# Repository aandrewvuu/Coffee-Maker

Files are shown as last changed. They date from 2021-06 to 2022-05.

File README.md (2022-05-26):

# Coffee Maker

As avid coffee consumers, we always wanted to try different techniques to make my coffee. Combining our love for coffee and my passion for engineering, we sought to automate pour over techinque to consistently create a delicious and flavourful coffee. This readme will act as a step by step guide as well as share our thought process while tackling this project.

## Preliminary Brainstorming

This is a brief overview of the logic behind this:

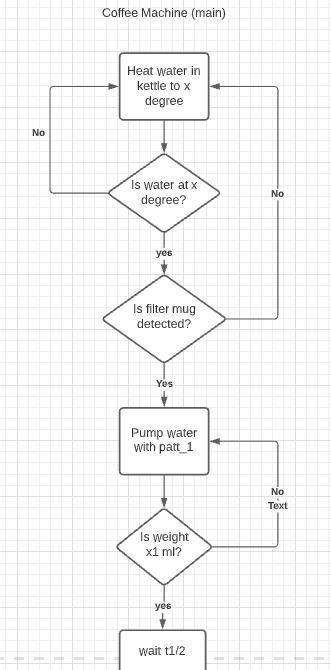
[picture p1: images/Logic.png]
 

This is a basic wiring diagram:

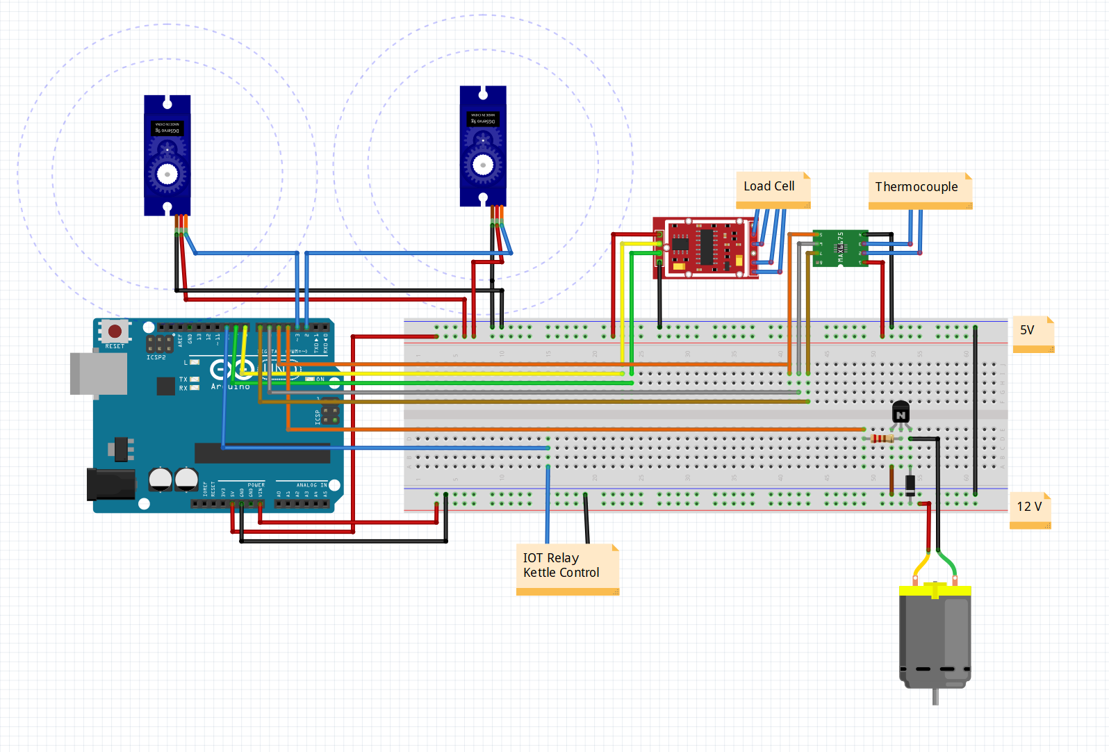
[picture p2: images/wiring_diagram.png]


## Bill of Materials

| Item | Amount | 
| -----|---|
|Arduino|1|
|IoT Relay|1|
|Pump|1|
|Kettle|1|
|Thermocouple|1|
|Load cell|1|
|Load cell ADC|1|
|Servo Motor|2|
|Plastic tubing|1|
|Copper Wire|1|
|Gasket|4|
|1/4 inch nuts|4|
|Brass nozzle fitting|1|
|Screws|8|

## Hardware Part

### Preparing the Kettle

1. Drill 2 1/4 inch holes at the bottom of the kettle with the holes being seperated by at least 1 inch.
2. Insert a rubber gasket onto the thermocouple and then insert it into the newly made holes in the kettle. Place a rubber gasket on the other side of the thermocouple and a 1/4 inch nut and tighten it so that the thermocouple is firmly secured.
3. Similiarly, place a rubber gasket onto the 1/4 inch brass nozzle fitting. Insert the fitting into the other kettle hole. Place a rubber gasket on the other side of the brass fitting and a 1/4 inch nut and tighten it so that the nozzle fitting is secured in place.

### Preparing the frame, nozzle system, and load cell

1. Connect a sufficient amount of food safe and heat tolerant plastic piping between brass nozzle fitting and the pump (must be able to handle boiling water).
2. Install the 2 servo motors with one servo motor installed to the arm of the second servo motor (refer to the image).
3. Connect plastic piping from the other end of the pump to the arm of the servo motor and tie it in place with a zip tie (again refer to the images).
4. Glue to the tip of the load cell onto a 5 inch diameter platform that the cup would be placed on. Glue to the other size of the load cell to a shim to raise the load cell of the ground (Images again).

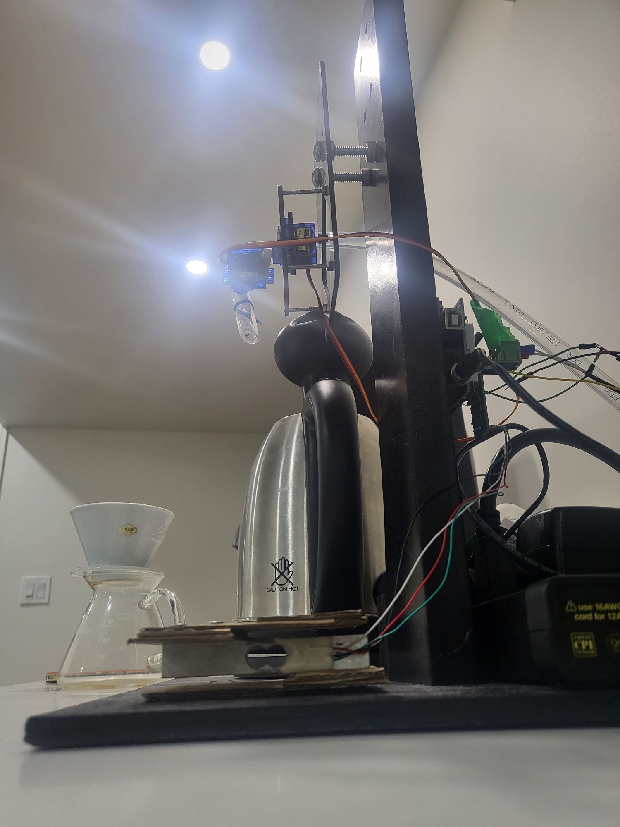
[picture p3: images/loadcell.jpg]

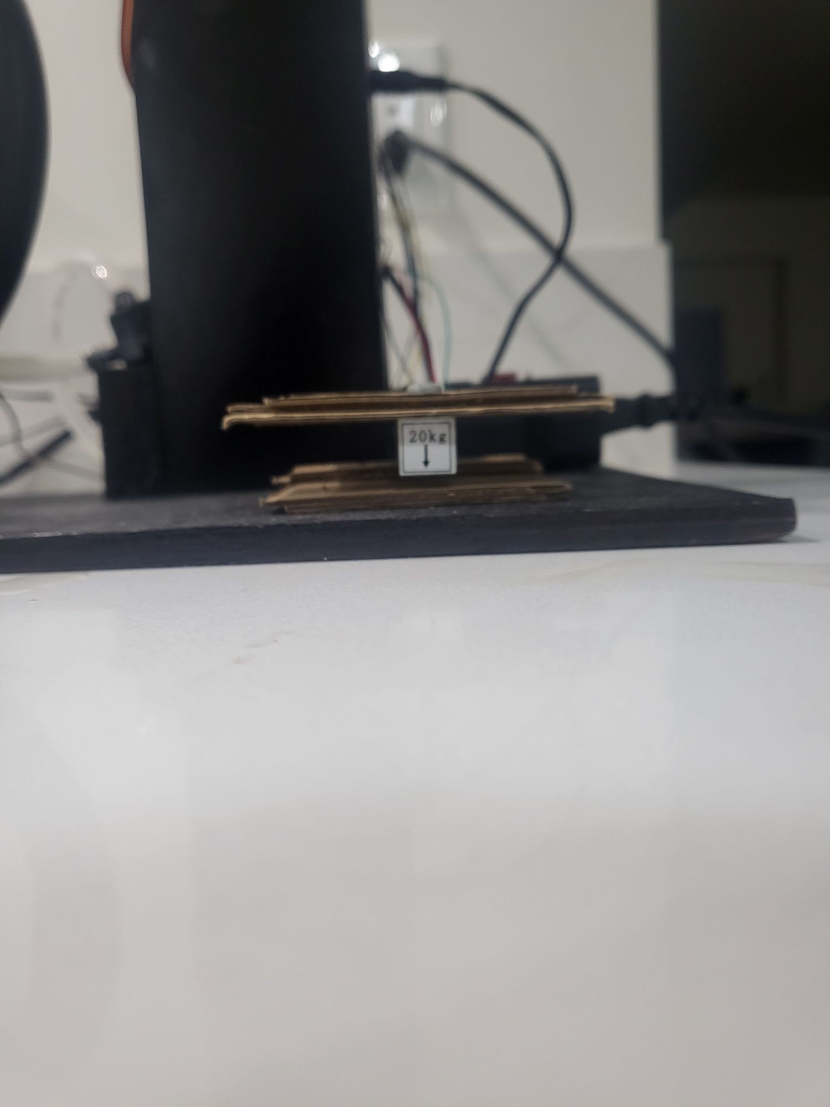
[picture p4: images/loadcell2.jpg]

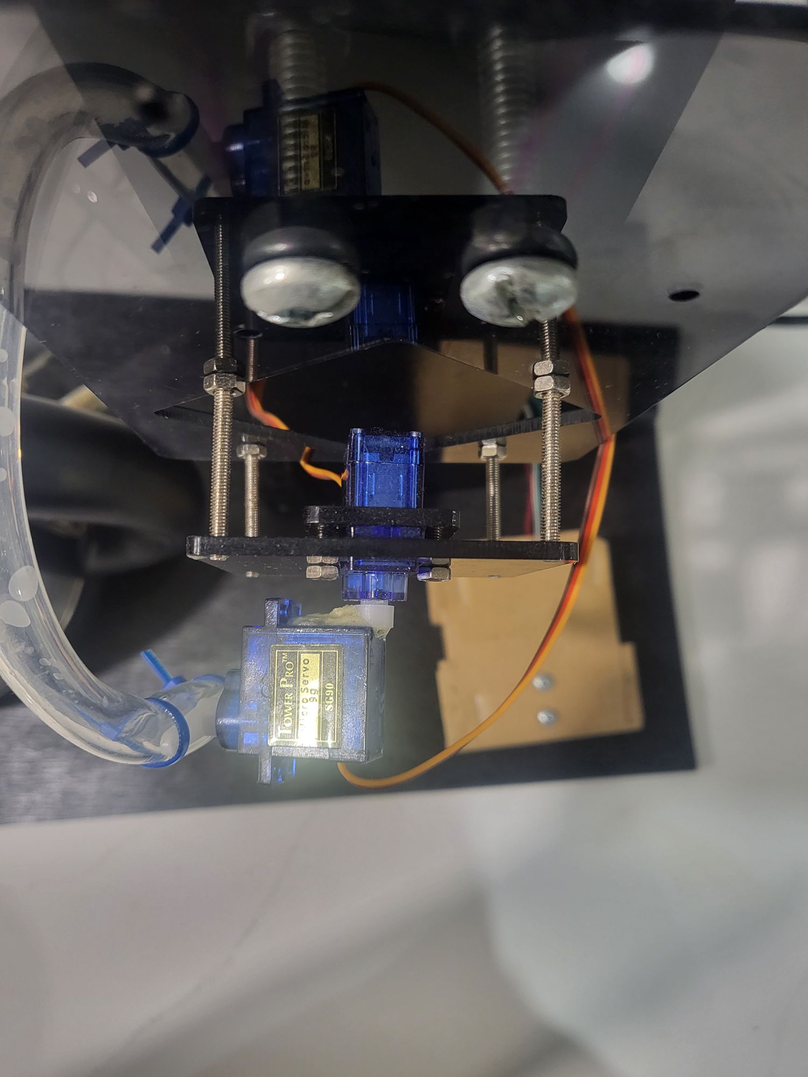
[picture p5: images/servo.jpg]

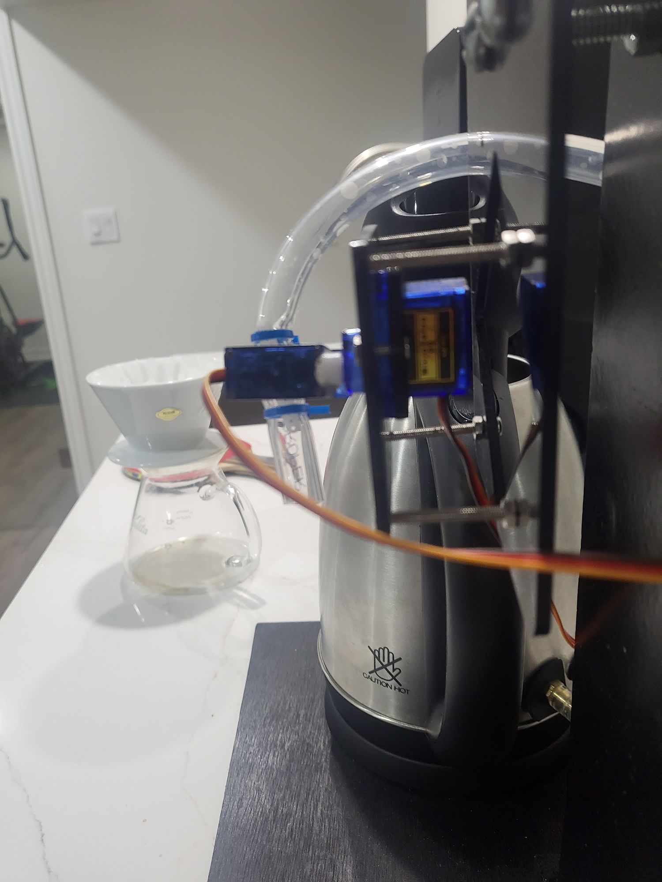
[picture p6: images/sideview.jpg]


### Wiring

Wire everything according to the wiring diagram provided with the Arduino being the center of it all.

## Software Part

The code is located at: Coffee-Maker/full_proj/full_proj.ino

## Conclusion

With the software and harware aspects of this project coming together, the coffee machine is complete and creates the most delicious coffee everyday.

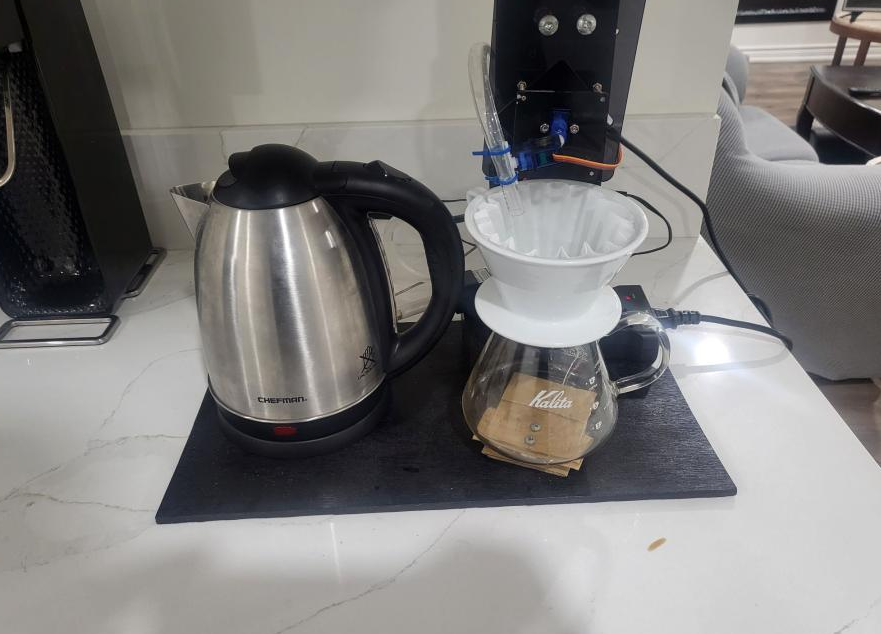
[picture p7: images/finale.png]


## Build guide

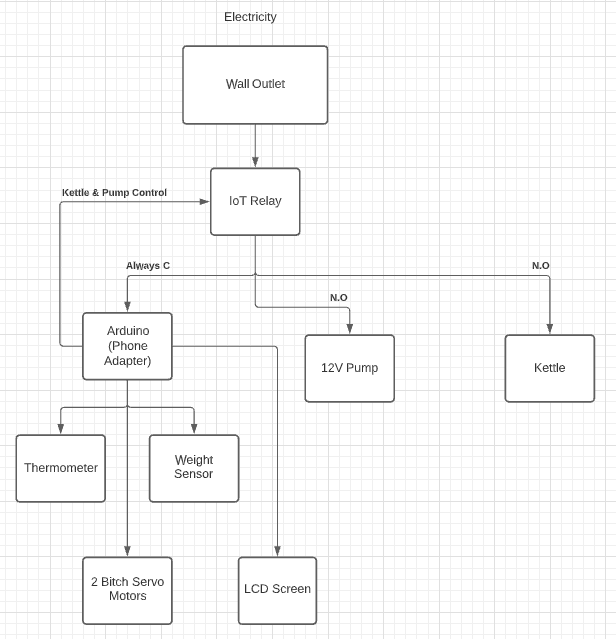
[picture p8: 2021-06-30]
images/Wiring.png

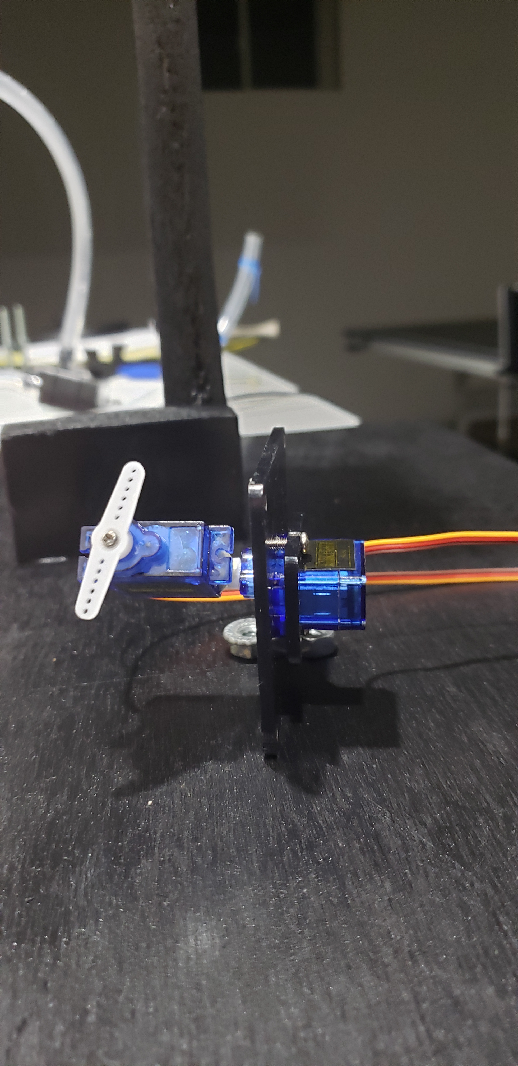
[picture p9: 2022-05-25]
images/Dispenser Assembly.jpg

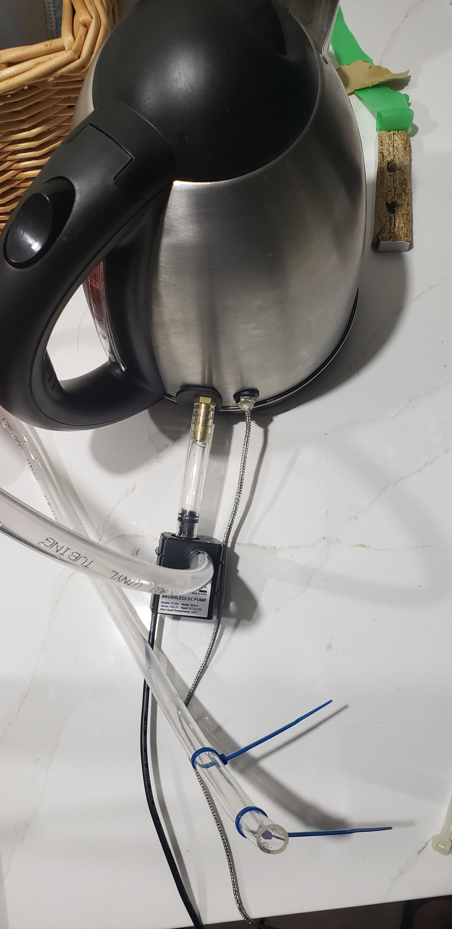
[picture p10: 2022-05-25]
images/Kettle Assembly.jpg

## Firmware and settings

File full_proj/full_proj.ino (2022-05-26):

#include <Servo.h>

#include <MAX6675_Thermocouple.h>
#include <SmoothThermocouple.h>
#include <Thermocouple.h>
#include <LiquidCrystal.h>
#include <Servo.h>
#include <math.h>

// Pins
int thermo_so_pin  = 10, thermo_cs_pin  = 9, thermo_sck_pin = 8;
int Xservo_pin = 2, Yservo_pin = 3;
int kettle_relay_pin = 5; 
int pump_relay_pin = 4;
int button_pin = 11, led_pin = 12;


// Constants
int radius1 = 30, radius2 = 15, radius3 = 0;
float target_temp = 90, temp =0;
//in millis
unsigned long duration1 = 3000, duration2 = 5000;
//duration 1000 is approximately 15ml of water

//Initialize Devices
Thermocouple* thermocouple;
Servo Xservo;
Servo Yservo;
  
void setup() {
  Serial.begin(9600);
  
  thermocouple = new MAX6675_Thermocouple(thermo_sck_pin, thermo_cs_pin, thermo_so_pin);
  Xservo.attach(Xservo_pin);
  Yservo.attach(Yservo_pin);
  pinMode(pump_relay_pin, OUTPUT);
  pinMode(kettle_relay_pin, OUTPUT);
  pinMode(led_pin, OUTPUT);
  pinMode(button_pin, INPUT_PULLUP);
  //initalizes pins to output or inputs
}


void loop() {
  temp_ctrl(kettle_relay_pin, target_temp);
  //stays in temp_ctrl function until the target temp is reached
  check_next(button_pin,led_pin);
  //check_next halts the loop until the next button is pressed. (for testing)
  servo_circle(Xservo, Yservo, radius1, duration2, pump_relay_pin);
  check_next(button_pin,led_pin);
  
  //below is for further testing 
  servo_circle(Xservo, Yservo, radius1, duration1, pump_relay_pin);
  check_next(button_pin,led_pin);
  servo_circle(Xservo, Yservo, radius1, duration2, pump_relay_pin);
  check_next(button_pin,led_pin);
  servo_circle(Xservo, Yservo, radius3, duration2, pump_relay_pin);
  exit(0);
}


void servo_circle(Servo Xservo, Servo Yservo, int radius, unsigned long duration, int pump_relay_pin){
  duration = duration + millis();
  boolean cycle = false;
  //duration is a constant timer. once the timer reaches the specified value from the 'duration' parameter, the circle stops and the pump stops 
  //(timing is controlled by motor_ctrl function)
  while(cycle == false){
    for (int i=0; i<360;i++){
      //using cos and sin, there are 2 servo motors moving in the X and Y directions. the correct X and Y position is written to the corresponding servo motor to create a circle
      double radians = 2*i * PI/180;
      double px = radius * cos(radians)+110;
      double py = radius * sin(radians)+90;
      Xservo.write(px);
      Yservo.write(py);
      Serial.print(px);
      Serial.print(py);
      Serial.print("\n");
      
      cycle = motor_ctrl(duration, pump_relay_pin);
      if (cycle == true) break;
      delay(5);
    }
  }
}

boolean motor_ctrl(unsigned long duration, int pump_relay_pin){
  unsigned long t = millis();
  if (duration > t){
    digitalWrite(pump_relay_pin, HIGH);
    return false;
  }
  else{
    digitalWrite(pump_relay_pin, LOW);
    return true;
  }
}

void temp_ctrl(int kettle_relay_pin, float target_temp){
  //kettle is on. thermocouple readback on arduino and turns off when kettle reaches temp
  while(temp < target_temp){
    temp = thermocouple->readCelsius();
    Serial.print(temp);
    Serial.print("\n");
    digitalWrite(kettle_relay_pin, HIGH);
    delay(500);
  }
  digitalWrite(kettle_relay_pin, LOW);
}

//int temp_check(int kettle_relay_pin, float target_temp){
//  temp = thermocouple->readCelsius();
//  Serial.print(val);
//  Serial.print("\n");
//  if (val < target_temp + 2) {
//    digitalWrite(kettle_relay_pin, HIGH);
//  }
//  
//  else if (val > target_temp - 2){
//    digitalWrite(kettle_relay_pin, LOW);
//  }
//
//  return temp;
//}



void check_next(int button_pin,int led_pin){
  int button_state = HIGH;
  while (button_state == HIGH){
    button_state = digitalRead(button_pin);
    digitalWrite(led_pin,HIGH);
    delay(10);
  }
  digitalWrite(led_pin,LOW);
}

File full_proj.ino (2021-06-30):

#include <Servo.h>

#include <AverageThermocouple.h>
#include <MAX6675_Thermocouple.h>
#include <SmoothThermocouple.h>
#include <Thermocouple.h>
#include <LiquidCrystal.h>
#include <Servo.h>
#include <math.h>

// Pins
int thermo_so_pin  = 10, thermo_cs_pin  = 9, thermo_sck_pin = 8;

int Xservo_pin = 2, Yservo_pin = 3;

int kettle_relay_pin = 7; 

int pump_relay_pin = 6;

//const int rs = 12, en = 11, d4 = 5, d5 = 4, d6 = 3, d7 = 2; 

// Constants
float temp = 0;
int radius = 45, target_temp = 90;
//in millis
unsigned long duration = 2000;

//Initialize Devices
//LiquidCrystal lcd(rs, en, d4, d5, d6, d7);
MAX6675_Thermocouple thermocouple(thermo_sck_pin, thermo_cs_pin, thermo_so_pin);
Servo Xservo;
Servo Yservo;
  
void setup() {
  Serial.begin(9600);
  

  Xservo.attach(Xservo_pin);
  Yservo.attach(Yservo_pin);

  
//  lcd.begin(16, 2);
//  // Print a message to the LCD.
//  lcd.print("hello, world!");
//  pinMode(thermo_vcc_pin, OUTPUT); 
//  pinMode(thermo_gnd_pin, OUTPUT); 
//  digitalWrite(thermo_vcc_pin, HIGH);
//  digitalWrite(thermo_gnd_pin, LOW);
}


void loop() {
  // set the cursor to column 0, line 1
  // (note: line 1 is the second row, since counting begins with 0):
//  lcd.setCursor(0, 1);

  temp = temp_ctrl(kettle_relay_pin, target_temp);

//  lcd.print(val);

  char input = check_next();

  servo_circle(Xservo, Yservo, radius, duration, pump_relay_pin);
  
}


void servo_circle(Servo Xservo, Servo Yservo, int radius, unsigned long duration, int pump_relay_pin){
  duration = duration + millis();
  int pos = 0;
  boolean cycle = false;
  while(cycle == false){
    for (int i=0; i<360;i++){
      
      double radians = i * PI/180;
      double px = radius * cos(radians)+90;
      double py = radius * sin(radians)+90;
      Xservo.write(px);
      Yservo.write(py);
      Serial.print(px);
      Serial.print(py);
      Serial.print("\n");
      
      cycle = motor_ctrl(duration, pump_relay_pin);
      if (cycle == true) break;
      delay(5);
    }
  }
}

boolean motor_ctrl(unsigned long duration, int pump_relay_pin){
  unsigned long t = millis();

  if (duration > t){
    digitalWrite(pump_relay_pin, HIGH);
    return false;
  }
  else{
    digitalWrite(pump_relay_pin, LOW);
    return true;
  }
}

int temp_ctrl(int kettle_relay_pin, int target_temp){
  int val = thermocouple.readCelsius();
  
  if (val < target_temp - 1) digitalWrite(kettle_relay_pin, HIGH);
  
  else if (val > target_temp + 1) digitalWrite(kettle_relay_pin, LOW);

  return val;
}

char check_next(){
  boolean go_next = false;
  char input;
  Serial.print("Press t to go next: \n");
  while (go_next == false){
    input = Serial.read();
    delay(5);
    if (input == 't') go_next = true;
  }
  return input;
}

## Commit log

2021-06-28 Project with temp_ctrl, servo_circle, motor_ctrl, check_next
2021-06-28 Adding features
    temp_ctrl, servo_circle, motor_ctrl, check_next
2021-06-28 Images for read me
    Adding flow charts
2021-06-29 Circuit Diagram
    [Coffee-Maker.fzz]
2021-06-29 clean up repo
    [Coffee-Maker.fzz]
2021-06-30 first test on prototype
2021-07-05 add button functionality
2021-07-08 working thermocouple and button ctrl
2022-05-26 Bill of materials Added
2022-05-26 Add breadboard schematic
    full wiring diagram with load cell/thermocouple/pump/relay
